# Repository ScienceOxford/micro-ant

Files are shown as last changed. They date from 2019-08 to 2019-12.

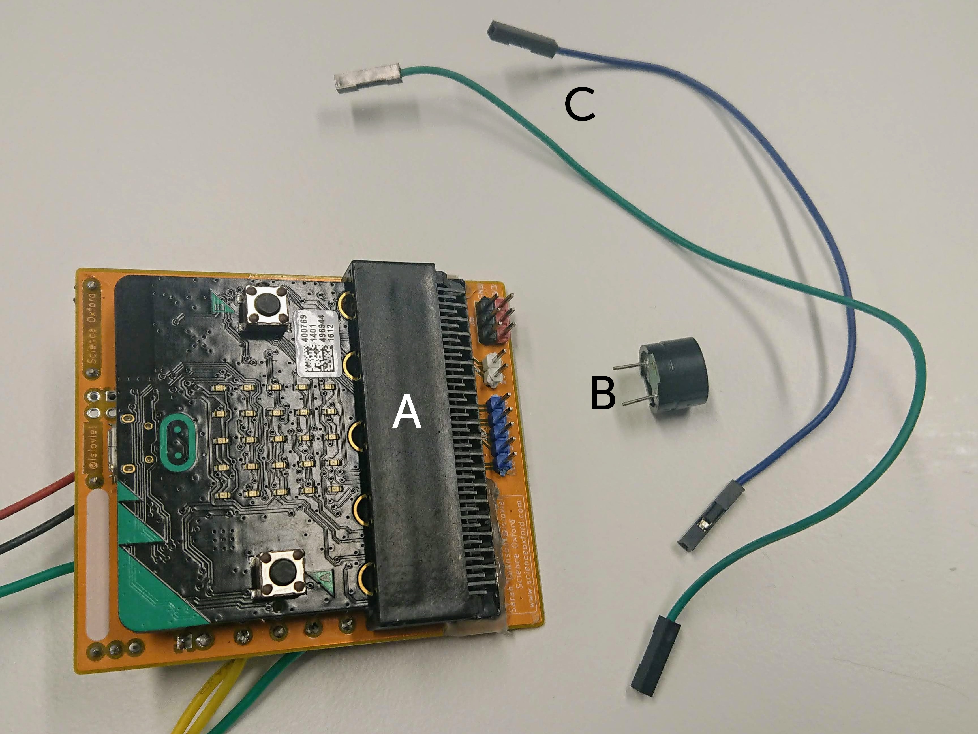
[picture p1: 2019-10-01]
docs/images/speaker_components.JPG

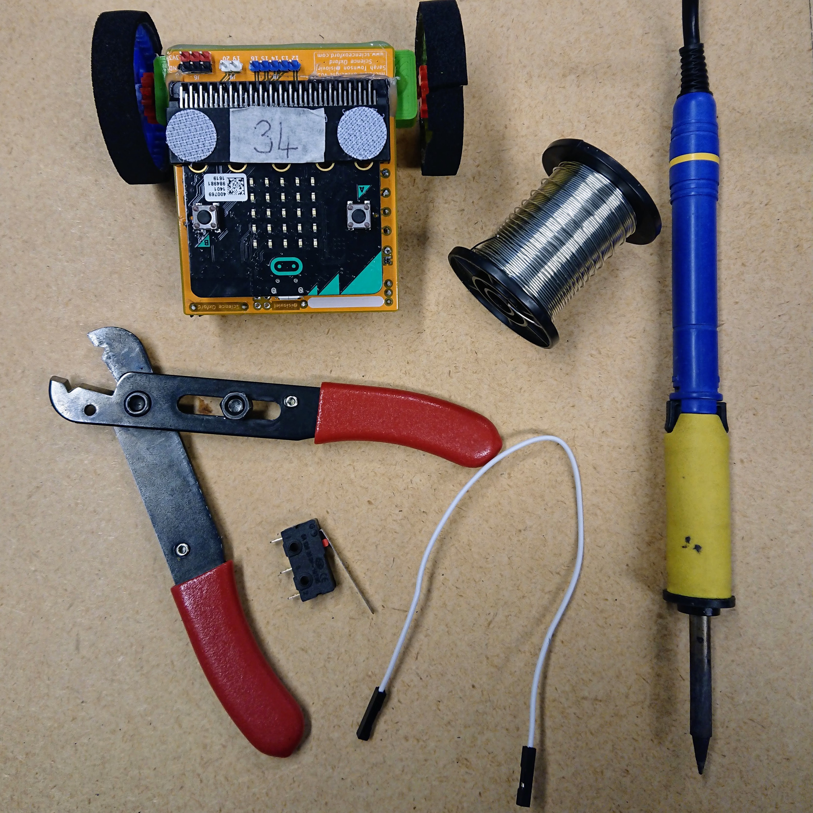
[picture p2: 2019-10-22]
docs/images/switch_components.JPG

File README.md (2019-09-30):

# micro-ant

### Click here to find all the information: <a href="https://scienceoxford.github.io/micro-ant" target="_blank">micro-ant</a>

Work in progress!

*Developed by [ScienceOxford](https://scienceoxford.com) for educational purposes. Please give credit where applicable.
<br>We love seeing what you've created, so tag us when you share! [@ScienceOxford](https://twitter.com/scienceoxford)*

<br />This work is licensed under a <a rel="license" href="http://creativecommons.org/licenses/by-sa/4.0/">Creative Commons Attribution-ShareAlike 4.0 International License</a>.

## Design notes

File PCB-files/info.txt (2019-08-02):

Added:
  Schematic
  Gerbers

To be added:
  Board file
  KiCad custom libraries & footprints
  Bill of Materials

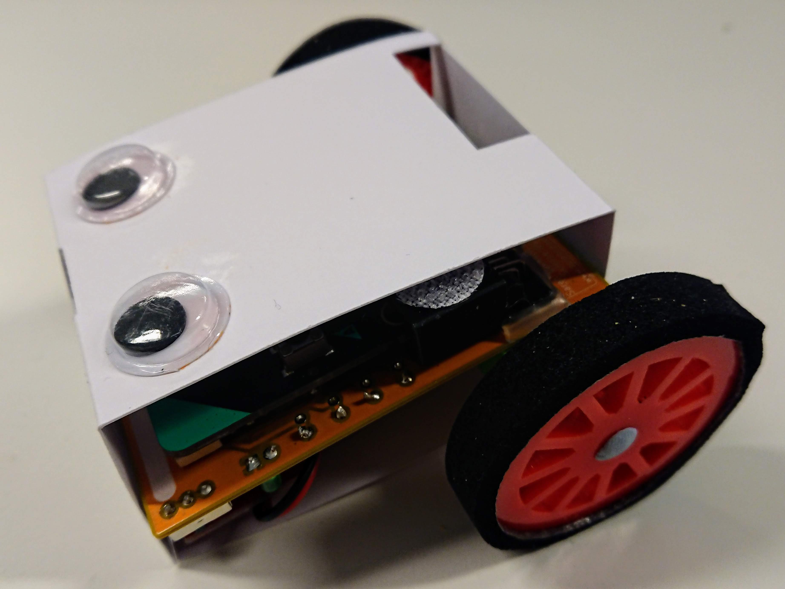
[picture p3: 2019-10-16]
docs/images/robot_body.JPG

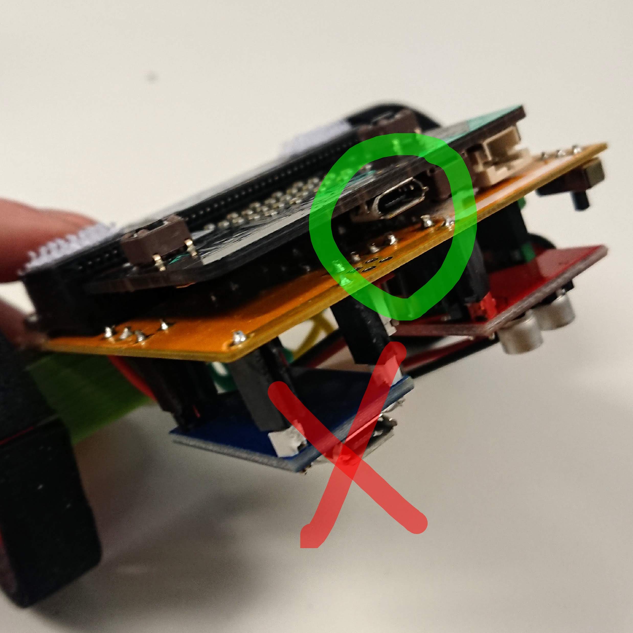
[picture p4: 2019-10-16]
docs/images/usb_ports.JPG

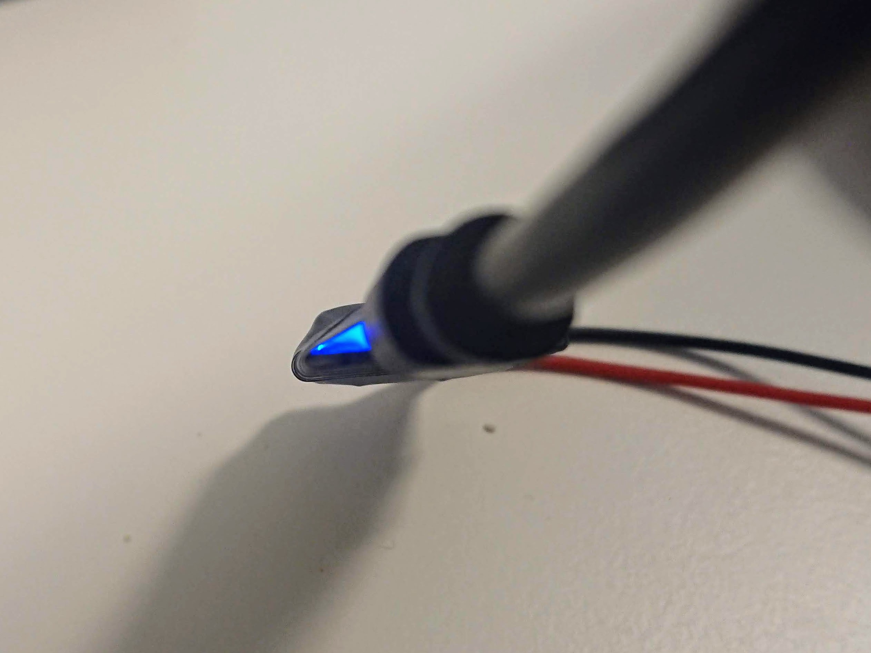
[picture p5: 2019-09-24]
docs/images/charging2.JPG

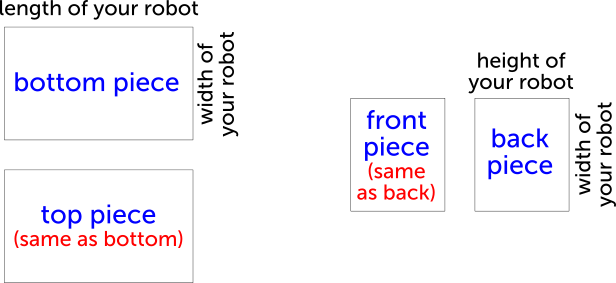
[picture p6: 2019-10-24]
docs/images/net-disconnected.png

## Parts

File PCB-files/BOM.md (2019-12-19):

# Bill of Materials

| Designator | Package | Quant | Designation | Example Supplier |
| --- | --- | ----- | --- | --- |
| C1, C2, C3 | C_Axial_L3.8mm_D2.6mm_P5.0mm_Horizontal | 3 | 1uF | <https://www.aliexpress.com/item/32848919879.html> |
| D1 | LED_3mm_Radial | 1 | |  |
| J1 | XH plug connector | 1 | | <https://www.aliexpress.com/item/32761581540.html> |
| J1 | 3.7V 1S LiPo Battery (XH plug) | 1 | | <https://www.aliexpress.com/item/32846780139.html> |
| J2, U1, U3 | Pin Header (Male) Straight Pitch 2.54mm | 18 | |  |
| J2 | Pin header jumper connector 2.54mm pitch | 1 | | <https://www.aliexpress.com/item/32827199777.html> |
| J3, J4 | Flexible wire ~24AWG | | |  |
| J3, J4 | N20 motor 3V ~300RPM | 2 | | <https://www.aliexpress.com/item/32913728217.html> |
| J5 | microbit_edge_connector (Kitronik) | 1 | | <https://www.kitronik.co.uk/4148-edge-connector-header-for-bbc-microbit.html> |
| J5 | Thick tape to raise the edge connector ~2mm | | |  |
| R1 | R_Axial_DIN0207_L6.3mm_D2.5mm_P7.62mm_Horizontal | 1 | 100 |  |
| S1 | slide_switch | 1 | | <https://www.amazon.co.uk/gp/product/B06XK9V582> |
| U1 | LipoCharger | 1 | | <https://www.aliexpress.com/item/32761199508.html> |
| U2 | TO-92-3 | 1 | MCP1700-3302E_TO92 | <https://www.aliexpress.com/item/32952835501.html> |
| U3 | MotorDriver | 1 | | <https://www.aliexpress.com/item/32646270295.html> |
| U4 | TO-92-3 | 1 | MCP1702-5002E_TO92 | <https://www.aliexpress.com/item/32849044125.html> |
| | BBC micro:bit | 1 | | <https://www.kitronik.co.uk/5615-bbc-microbit-starter-kit.html> |
| C4, C5 | C_Axial_L3.8mm_D2.6mm_P5.0mm_Horizontal | 1 | 1uF | OPTIONAL |
| J3, J4 | C_Axial_L3.8mm_D2.6mm_P5.0mm_Horizontal | 1 | 0.1uF | OPTIONAL |
| J6, J8, J9, J10a | Pin Header (Male) Straight Pitch 2.54mm | 15 | | OPTIONAL |
| J7, J10b | external battery and appropriate connector cable | 1 | | OPTIONAL |
| U1, U3 | Pin Header (Female) Straight Pitch 2.54mm | 16 | | OPTIONAL |

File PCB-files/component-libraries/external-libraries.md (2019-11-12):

# Also add the following libraries

Edge connector pins: https://github.com/anthonykirby/kicad_microbit_connector/tree/master/lib_microbit_connector
Slide swich: https://github.com/Digi-Key/digikey-kicad-library/tree/master/digikey-symbols

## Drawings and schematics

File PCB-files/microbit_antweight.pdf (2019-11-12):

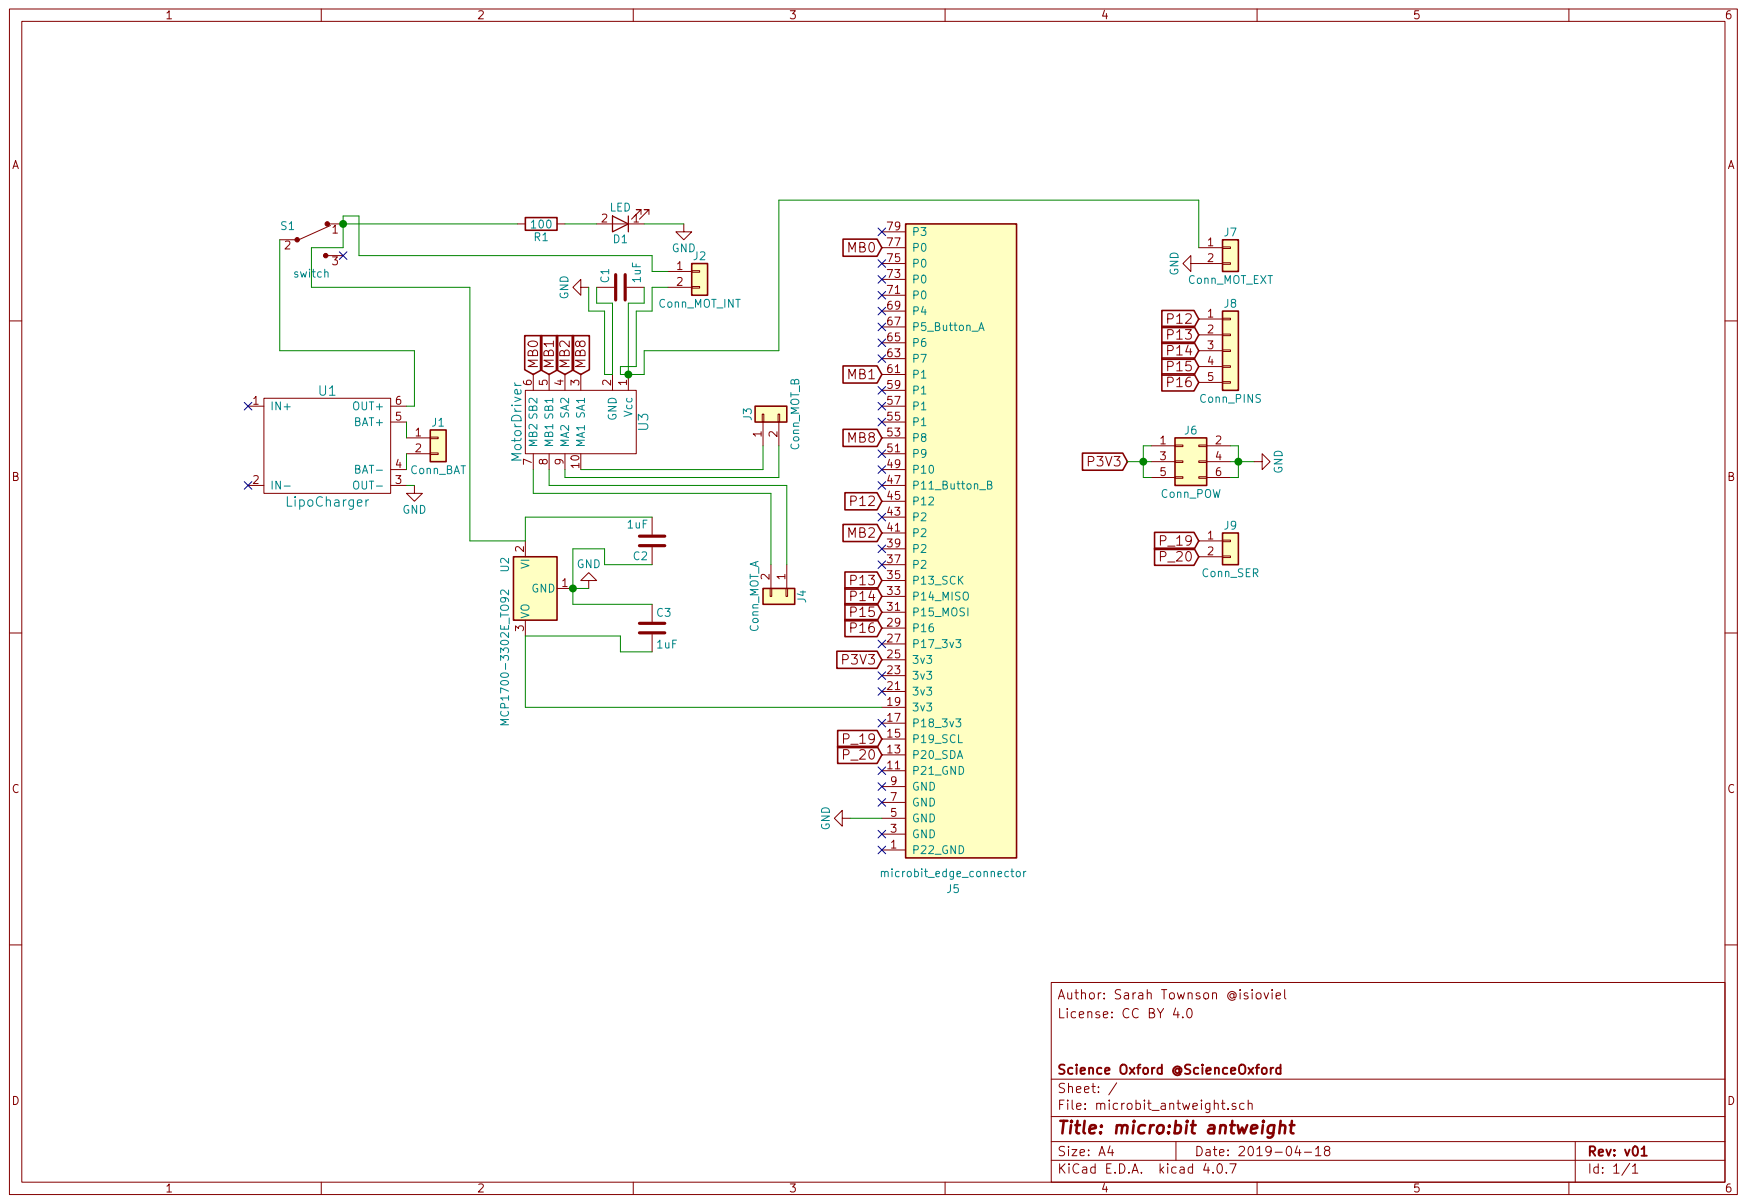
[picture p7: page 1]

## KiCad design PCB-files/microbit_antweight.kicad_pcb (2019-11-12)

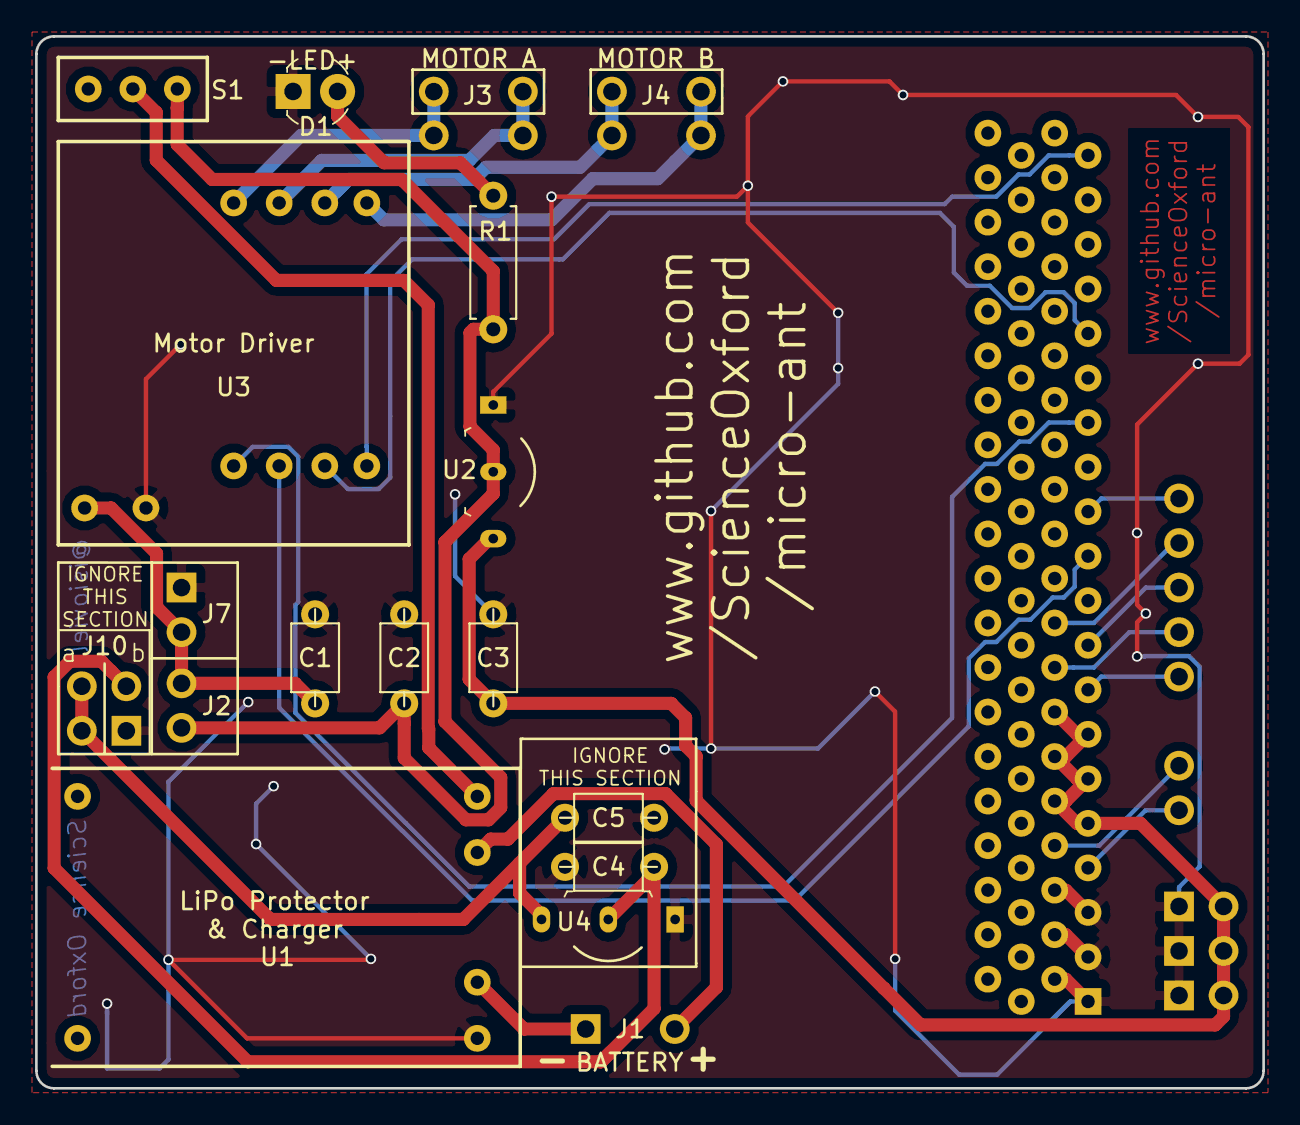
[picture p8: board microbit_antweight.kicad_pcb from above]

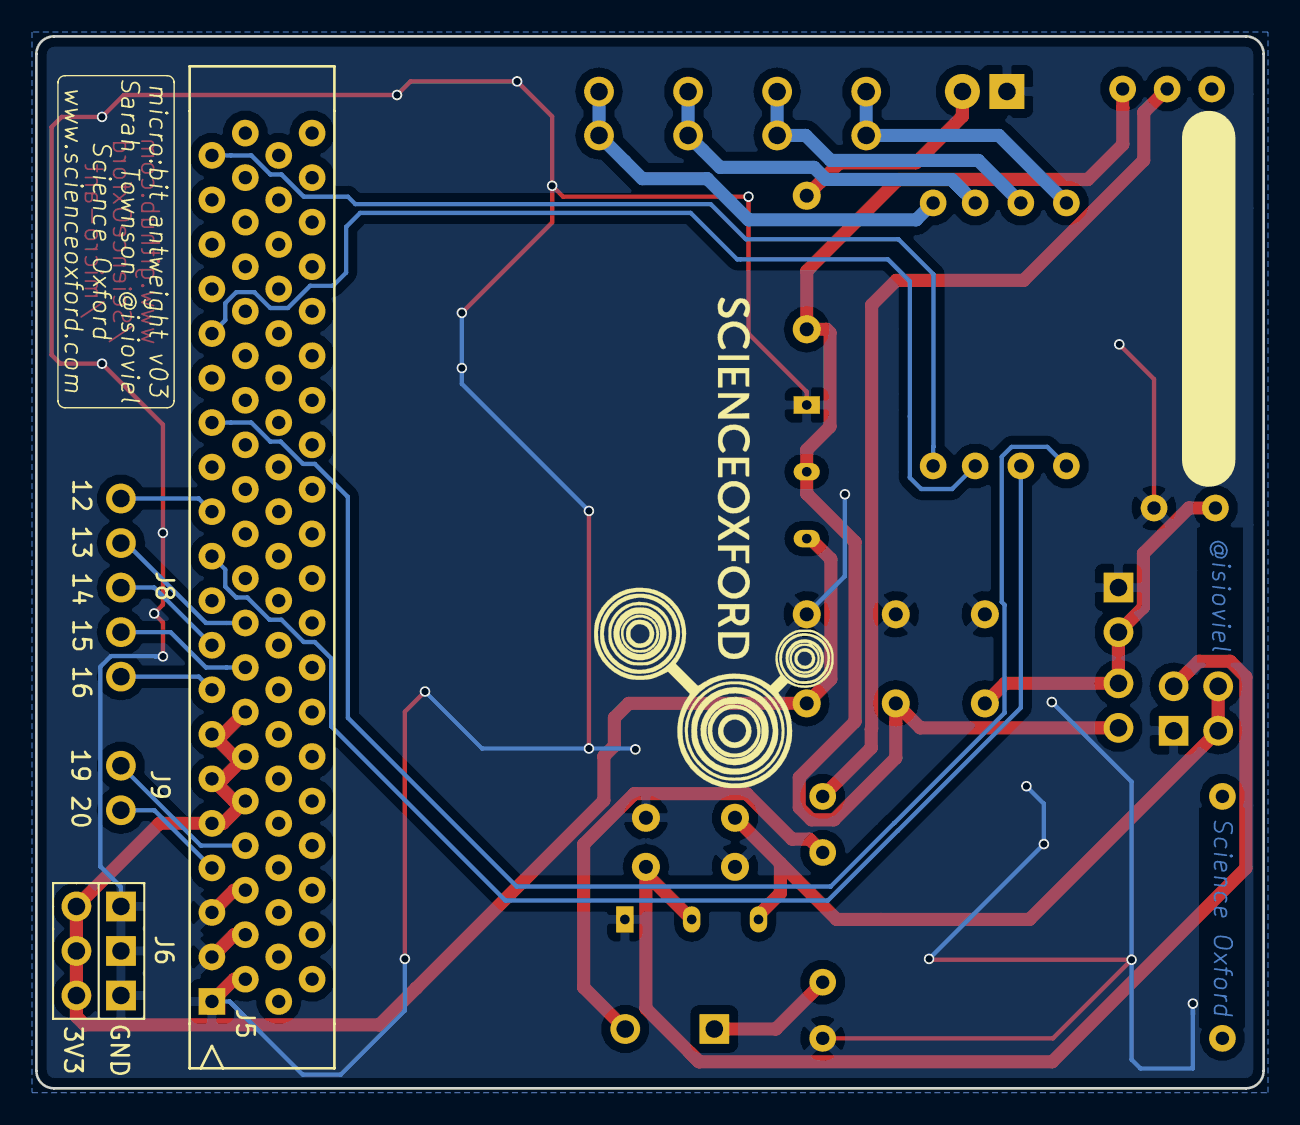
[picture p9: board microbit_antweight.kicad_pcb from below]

Board: 2 copper layers, 70.0 x 60.0 mm, 22 parts (4 on the bottom side), 25 nets.

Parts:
C1, C2, C3, C4, C5: 1uF; C_Axial_L3.8mm_D2.6mm_P5.0mm_Horizontal
D1: LED; LED_3mm_Radial
J1: Conn_BAT; Pin_Header_Straight_1x02_Pitch_large_battery
J2: Conn_MOT_INT; Pin_Header_Straight_1x02_Pitch2.54mm
J3: Conn_MOT_B; Pin_Header_Straight_1x02_Pitch_large_doubled
J4: Conn_MOT_A; Pin_Header_Straight_1x02_Pitch_large_doubled
J5: microbit_edge_connector
J6: Conn_POW; Pin_Header_Straight_2x03_Pitch2.54mm
J7: Conn_MOT_EXT; Pin_Header_Straight_1x02_Pitch2.54mm_battery
J8: Conn_PINS; Pin_Header_Straight_1x05_Pitch2.54mm
J9: Conn_SER; Pin_Header_Straight_1x02_Pitch2.54mm
J10: Conn_REG; Pin_Header_Straight_2x02_Pitch2.54mm
R1: 100; R_Axial_DIN0207_L6.3mm_D2.5mm_P7.62mm_Horizontal
S1: switch; slide_switch
U1: LipoCharger
U2: MCP1700-3302E_TO92; TO-92-3
U3: MotorDriver
U4: MCP1702-5002E_TO92; TO-92-3

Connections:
5V: C5.1, J10.1, J10.3, U4.3
GND: C1.1, C2.1, C3.1, C4.1, C5.2, D1.1, J5.1, J5.3, J5.5, J5.7, J5.9, J5.11, J6.2, J6.4, J6.6, J7.2, J10.4, U1.3, U2.1, U3.2, U4.1
MB0: J5.77, U3.6
MB1: J5.61, U3.5
MB2: J5.41, U3.4
MB8: J5.53, U3.3
unnamed: C1.2, J2.2, J7.1, U3.1
unnamed: C2.2, J2.1, R1.2, S1.1, U2.2
unnamed: C4.2, J10.2, U4.2
unnamed: D1.2, R1.1
unnamed: J1.1, U1.5
unnamed: J1.2, U1.4
unnamed: J3.1, U3.10
unnamed: J3.2, U3.9
unnamed: J4.1, U3.8
unnamed: J4.2, U3.7
unnamed: S1.2, U1.6
P3V3: C3.2, J5.17, J5.19, J5.21, J5.23, J5.25, J5.27, J6.1, J6.3, J6.5, U2.3
P12: J5.45, J8.1
P13: J5.35, J8.2
P14: J5.33, J8.3
P15: J5.31, J8.4
P16: J5.29, J8.5
P_19: J5.15, J9.1
P_20: J5.13, J9.2

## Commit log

2019-10-01 added pin soldering instructions
2019-10-02 add some soldering images
2019-10-22 robocamp-followup
    add servo & bumper instructions
2019-11-12 v3 pcb files
    Added schematic + board files, custom libraries & bill of materials
    [microbit_antweight.kicad_pcb, microbit_antweight.sch]
2022-07-08 Update joystick_working+buttons.py
    update button range
2022-07-08 Update joystick_working.py
    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
2022-07-08 Update joystick_buttons.py
    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
2022-07-08 Update joystick_left_right.py
    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
2022-07-08 Update joystick_setup.py
    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

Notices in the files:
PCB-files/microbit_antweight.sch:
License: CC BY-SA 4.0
